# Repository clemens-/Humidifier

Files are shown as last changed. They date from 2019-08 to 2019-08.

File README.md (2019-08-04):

# Automatic cigar humidifier
This is a device to control the humidity in a humidor for storing cigars.

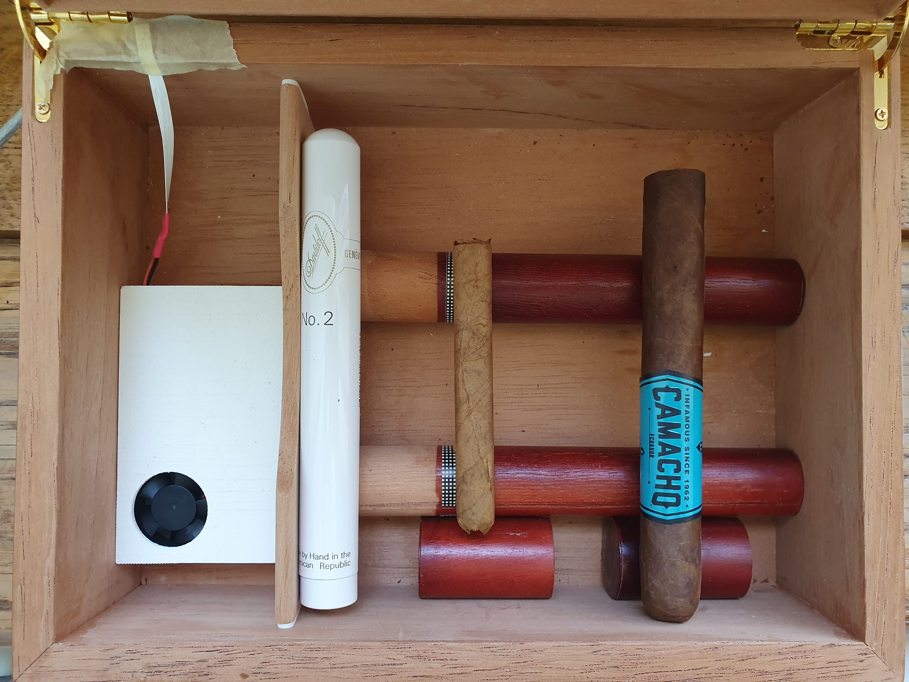
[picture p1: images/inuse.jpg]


## The idea
I enjoy smoking a cigar from time to time. However, cigars need to be stored at a controlled humidity level until it is time to enjoy them. So, I bought a cheap humidor with a passive element in it for just that. A passive element works be releasing humidity until a certain relative humidity is reached but can also absorb excess humidity. In my case, this did not work properly: the foam would never reach the desired percentage of relative humidity. Thus, I set out to solve this issue.
## Defining requirements
I first defined some requirements before starting anything:
* The relative humidity should be actively controlled.
* The device should fit inside the humidor.
* If the humidity cannot be controlled for whatever reason, the user shall notice.
* No batteries to worry about.
## The solution
The device I built uses a humidity sensor (the SHT-31 by Sensirion), a fan and a piece of foam soaked in distilled water. If the sensor notices that the humidity drops below a certain threshold, the fan is switched on. It blows air over the wet foam, thus humidifying the air and raising the humidity inside the humidor. After the upper humidity threshold is reached, the fan is switched off. An integrated speaker alerts the user if the humidity cannot be raised after a certain time. The humidifier fits inside the humidor and is powered by a 5V USB charger, plugged into an outlet near the humidor.

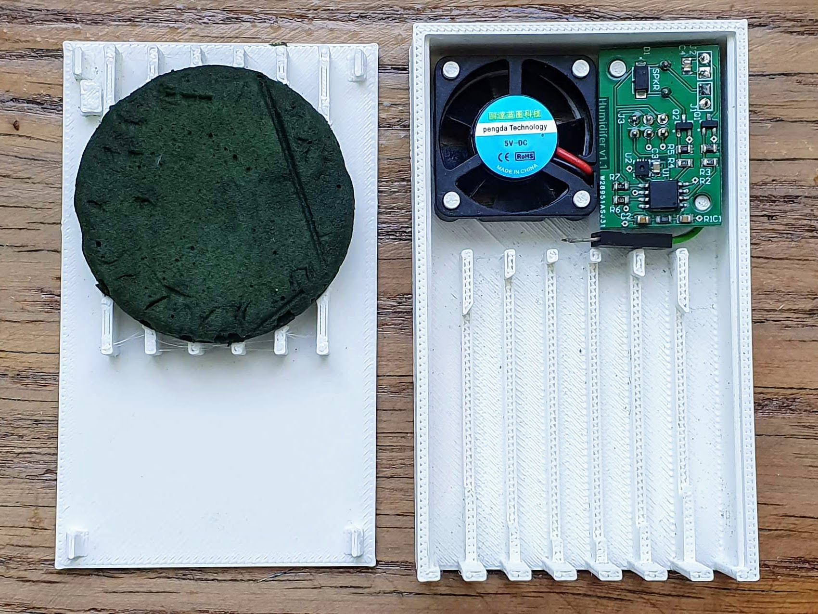
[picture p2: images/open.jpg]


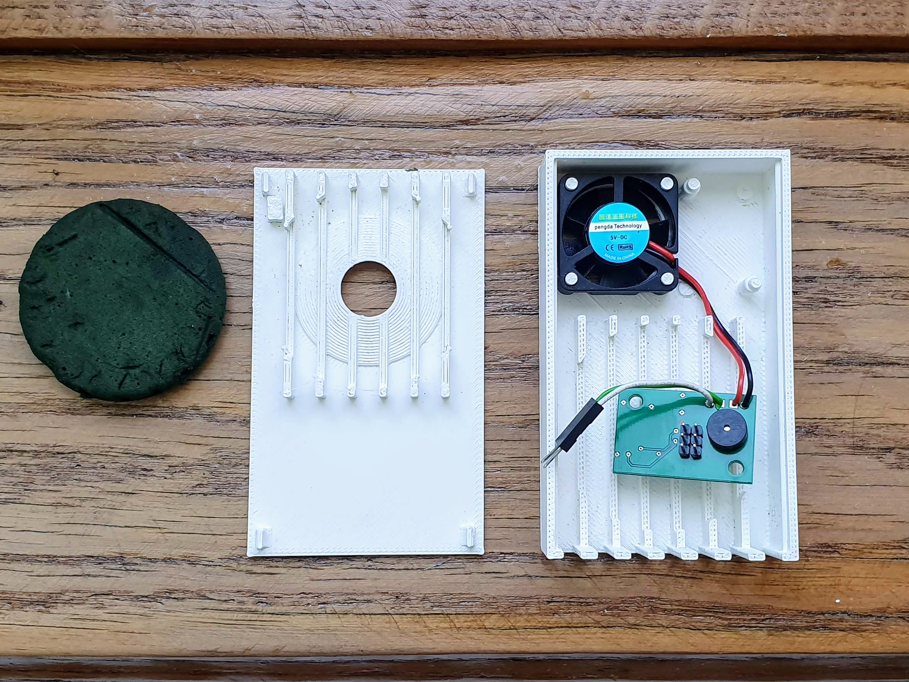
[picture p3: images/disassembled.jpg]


## Testing
I have been using the humidifier in my humidor for about 6 months now with two Sensirion humidity and temperature measurements devices in the two compartments. The relative humidity setpoint is at 77%. As you can see below, this is kept quite closely.

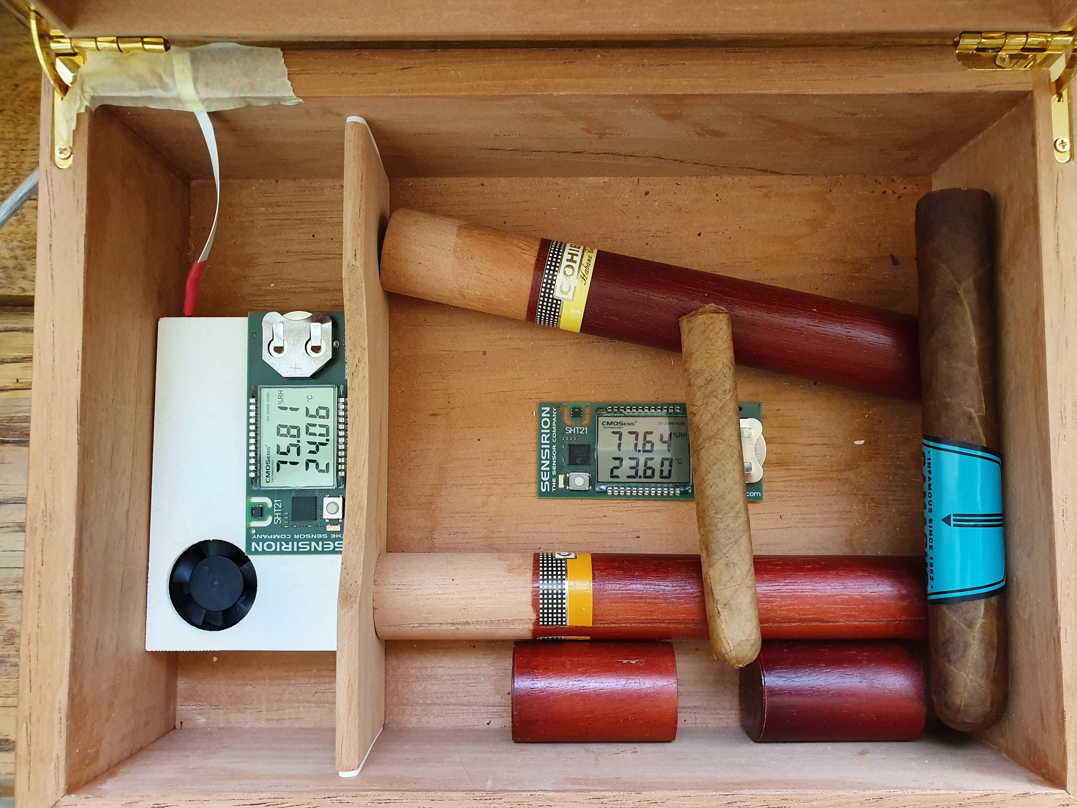
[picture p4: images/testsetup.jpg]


## Improvements
I already noticed some possible improvements, but did not implement them as the humidifier works quite well:
1. The alarm is not often triggered, hence not that noticeable. However, triggering the alarm more often could be very annoying, as there is nothing in there preventing it from going off at 2 in the morning.
2. The fan control is only ON-OFF. A PWM control would help in making the device a bit quieter than it currently is. It is not loud, but noticeable in a quiet room.
3. The foam I used is not very absorbable. Thus, when filling the funnel in the back, the water runs over the foam and into the rest of the enclosure. A more absorbable foam should resolve that. Alternatively, extending the funnel into the foam would allow a more controlled water path.
## What is in the repository?
I documented my work here and I think it should be self-explanatory. Here is an overview:
### BOM
The bill of materials lists all the material used for building the humidifier. For the fan, just use any generic 30mm 5V fan. I got mine of AliExpress.
### Enclosure
The enclosure I designed holds the fan, PCB and the piece of 50mmx10mm foam I used to store the distilled water. It consists of the following parts:
* The cover clips into the enclosure and has a funnel to soak the foam without taking the cover off.
* The enclosure which has stubs to mount the fan, the PCB and the foam.
* Standoffs I needed to lift the PCB after I realised that it was sitting too low.

All are available as STLs, so you can directly 3D print them. I also included the Fusion 360 project as an F3Z file. I printed the parts on my Cetus 3D and they turned out great, with the clipping action holding up to several cycles so far.
### Images
Some images of the humidifier. They are also used in this readme.
### PCB
Contains the Gerber and NG Drill files you need if you want to build this humidifier.
### Schematics
The schematic is stored here. If you open it in Adobe Reader, you can even click the parts to reveal more information.
### Software
The Arduino software is stored here. You will need to load the Arduino bootloader onto the ATiny85 before using it. Check [SpenceKonde's ATTinyCore](https://github.com/SpenceKonde/ATTinyCore) on how to do this.

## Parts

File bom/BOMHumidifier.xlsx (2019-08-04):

Designator | Quantity | Comment | Description | Footprint
C1, C2, C3, C4 | 4 | Capacitor - 0805 | A generic 0805 capacitor | 0805
D1 | 1 | CGRA4007-G | DIODE GEN PURP 1KV 1A DO214AC | DO-214AC
J1, J2 | 2 | Würth Elektronik 61300211121 | THT Vertical Pin Header WR-PHD, Pitch 2.54 mm, Single Row, 2 pins | 1x2P
J3 | 1 | TE Connectivity (Tyco Electronics) 826632-3 | Conn Unshrouded Header HDR 6 POS 2.54mm Solder ST Thru-Hole Automotive Carton | 2x3P
Q1, Q2 | 2 | International Rectifier IRLML2502TRPBF | MOSFET MOSFT 20V 4.2A 45mOhm 8nC Log Lvl | SOT-23-NB3_M
R1, R2, R3, R4, R5, R6, R7 | 7 | RES0805 | Generic 0805 Resistor | 0805
SPKR | 1 | PUI Audio AI-1027-TWT-5V-2-R | Audio Indicator Indicator Piezo 30mA Pin 3Vdc 2430Hz to 3030Hz Through Hole | AI-1027-TWT-5V-2-R
U1 | 1 | ATtiny85-20SU | 8-bit AVR Microcontroller, 20MHz, 2.7-5.5V, 8K Flash, 512 Bytes EEPROM, 512 Bytes SRAM, Industrial Grade (-40°C to 85°C), 8-Lead SOIC, Pb-Free | SOIC8
U2 | 1 | Sensirion SHT31-DIS-B | Humidity Sensor, 2 %, 3.3 V, 0% to 100% Relative Humidity, TDFN, 125 C, 8 | SHT31
Fan | 1 | pengda 3010 | 30x30x10mm Fan, 5V | 30x30mm

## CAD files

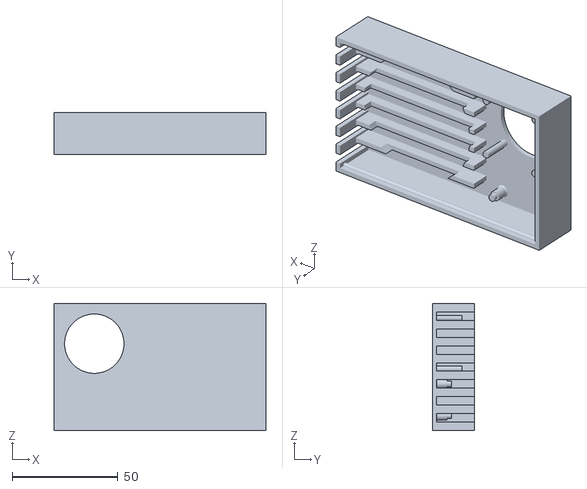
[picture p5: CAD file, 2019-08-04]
enclosure/enclosure.stl
100.0 x 20.0 x 60.0

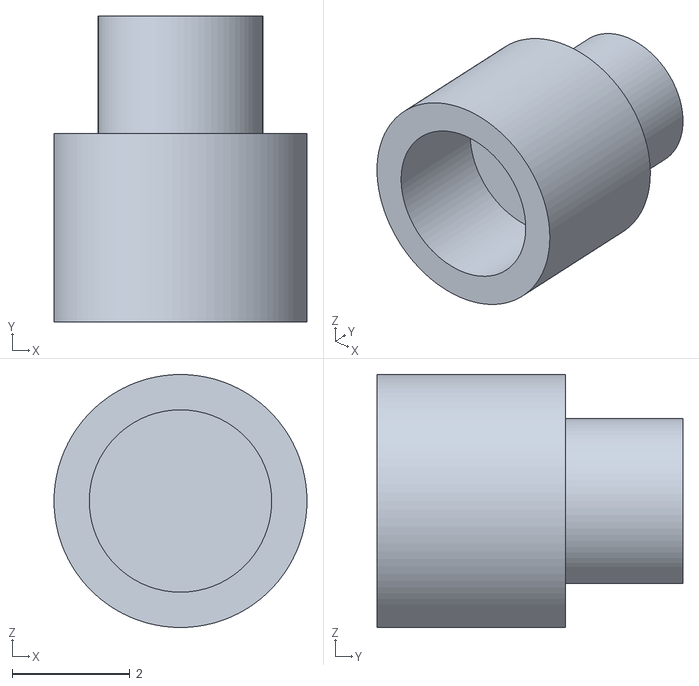
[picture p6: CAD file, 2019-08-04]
enclosure/pcbstandoff.stl
4.30 x 5.20 x 4.30

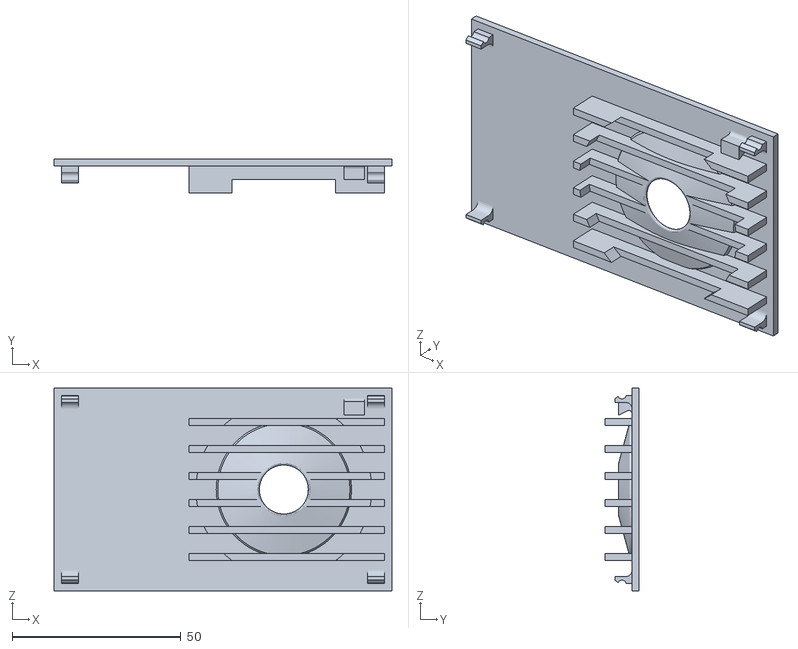
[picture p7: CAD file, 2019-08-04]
enclosure/cover.stl
100.0 x 10.0 x 60.0

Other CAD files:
enclosure/Humidifier.f3z

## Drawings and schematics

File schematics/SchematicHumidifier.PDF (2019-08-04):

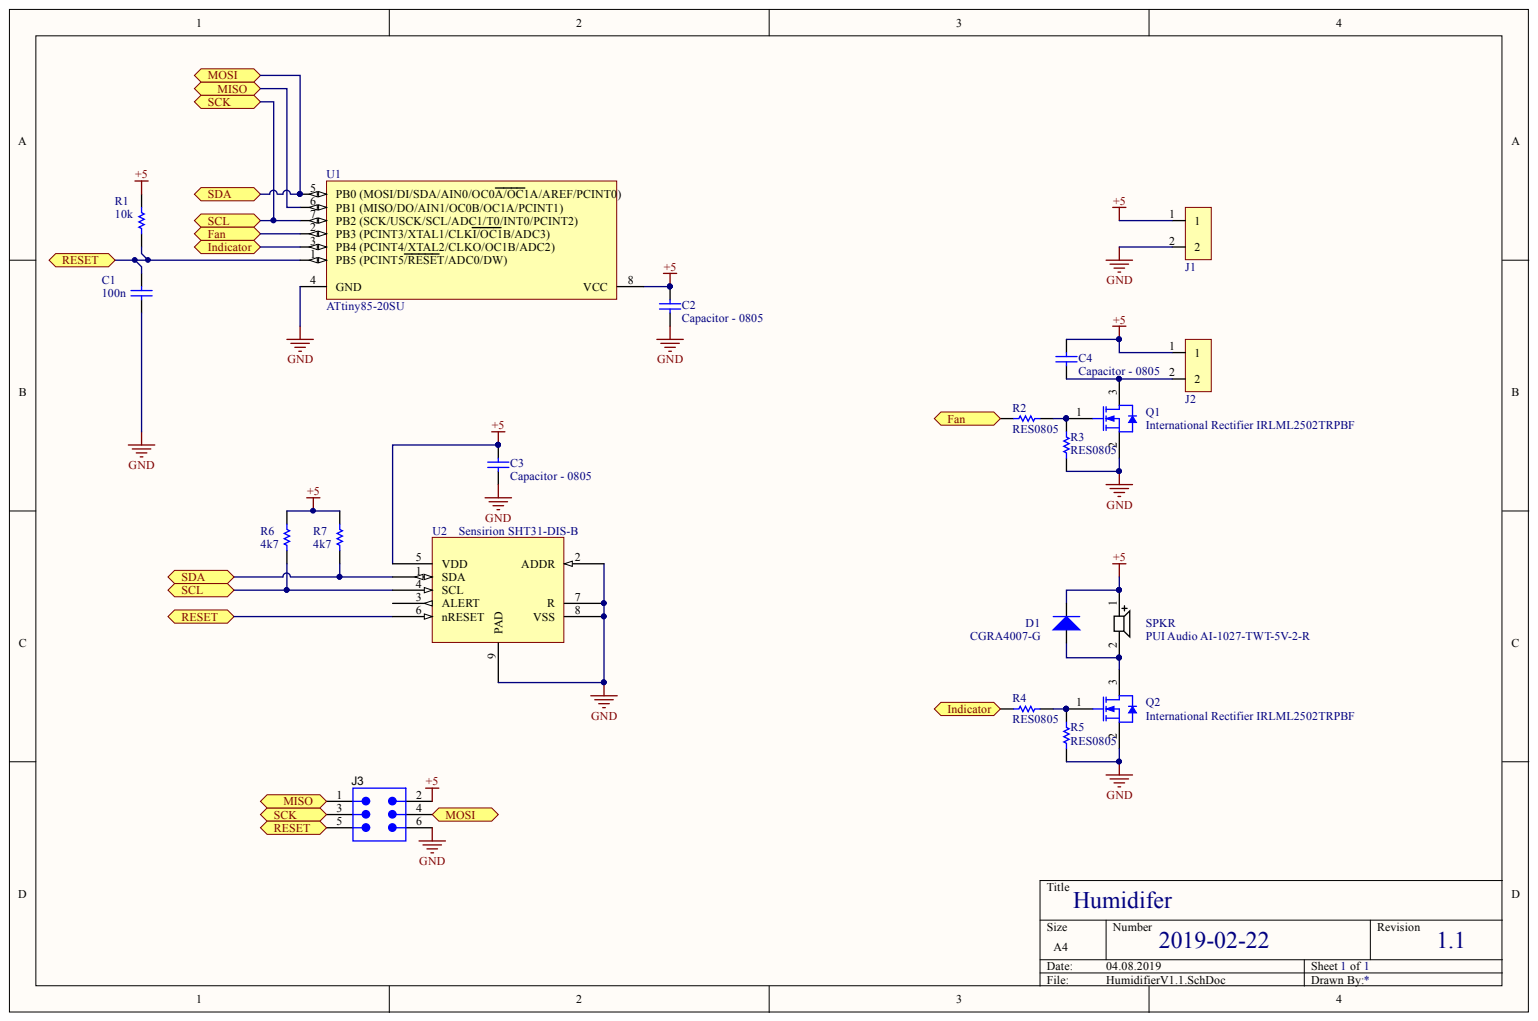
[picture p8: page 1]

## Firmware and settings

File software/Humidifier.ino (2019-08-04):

/*
 * Copyright 2019 Clemens Clausen
 * 
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
 * You should have received a copy of the GNU General Public License
 * along with this program.  If not, see <http://www.gnu.org/licenses/>.
*/

// Uses the send-only serial library by Nick Gammon and the 
// arduino-sht library by Sensirion
// https://github.com/nickgammon/SendOnlySoftwareSerial
// https://github.com/Sensirion/arduino-sht/blob/master/SHTSensor.h
#include <SendOnlySoftwareSerial.h>
#include <Wire.h>
#include "SHTSensor.h"

#define HUMREF 65 // Reference value for the humidity
#define HUMHYST 3 // Tolerance for the humidity, +- HUMHYST %RH
#define MAXALARMCOUNTS 3600
#define FAN PIN_B3
#define IND PIN_B4

SendOnlySoftwareSerial mySerial(PIN_B1);  // Tx pin

// SHTSensor sht;
// To use a specific sensor instead of probing the bus use this command:
SHTSensor sht(SHTSensor::SHT3X);

uint16_t alarm_counter = 0;

void setup() {
  // Set the fan and indicator pins
  pinMode(FAN, OUTPUT);
  digitalWrite(FAN, LOW);
  pinMode(IND, OUTPUT);
  digitalWrite(IND, HIGH);
  delay(50);
  digitalWrite(IND, LOW);
  // Start the serial connection
  mySerial.begin(115200);
  delay(100);
  // Start the I2C/TWI interface
  Wire.begin();
  // Try to init the humidity sensor
  if (sht.init()) {
      mySerial.println("init(): success");
  } else {
      mySerial.println("init(): failed");
  }
  sht.setAccuracy(SHTSensor::SHT_ACCURACY_HIGH); // only supported by SHT3x
}

void loop() {  
  // Get the current humidity and temperature values
  if (sht.readSample()) {
    // Send to serial connection for debug
    mySerial.print("RH: ");
    mySerial.print(sht.getHumidity(), 2);
    mySerial.print("  T: ");
    mySerial.println(sht.getTemperature(), 2);
    
    // Decide whether the fan should be switched on to increase humidity
    if(sht.getHumidity() < (HUMREF - HUMHYST)) {
      digitalWrite(FAN, HIGH);
      alarm_counter++;
      mySerial.print("Alarm: ");
      mySerial.println(alarm_counter);
    } else if (sht.getHumidity() > (HUMREF + HUMHYST)) {
      digitalWrite(FAN, LOW);
      alarm_counter = 0;
//      WDT_Initialization_as_Wakeup_Source();
    }
    
    // If the alarm counter increases, do periodic pauses to check the actual humidity
    if( (alarm_counter % (MAXALARMCOUNTS / 8)) == 0) {
      digitalWrite(FAN, LOW);
      delay(30000);
    }

    
    // Check if the humidity cannot increase and sound the alarm once
    if(alarm_counter >= MAXALARMCOUNTS) {
      alarm_counter = 0;
      digitalWrite(IND, HIGH);
      delay(500);
      digitalWrite(IND, LOW);
      delay(500);
      digitalWrite(IND, HIGH);
      delay(500);
      digitalWrite(IND, LOW);
      delay(500);
    }
  } else {
    // If the sensor cannot be read, sound a different alarm
    mySerial.println("Error in readSample()");
    digitalWrite(IND, HIGH);
    delay(200);
    digitalWrite(IND, LOW);
    delay(200);
    digitalWrite(IND, HIGH);
    delay(200);
    digitalWrite(IND, LOW);
    delay(200);
    digitalWrite(IND, HIGH);
    delay(200);
    digitalWrite(IND, LOW);
  }
  // Wait 1 seconds before the next measurement
  delay(1000);
}

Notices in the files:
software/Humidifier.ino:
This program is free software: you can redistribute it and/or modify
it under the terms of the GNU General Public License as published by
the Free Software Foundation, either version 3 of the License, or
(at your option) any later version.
